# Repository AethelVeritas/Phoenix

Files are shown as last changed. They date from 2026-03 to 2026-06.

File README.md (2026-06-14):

<div align="center">
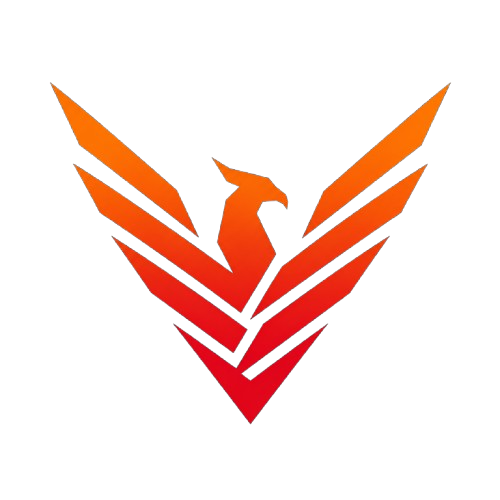
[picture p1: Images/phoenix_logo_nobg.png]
Phoenix Logo
  
  <h1>Phoenix</h1>
</div>

    
Like the mythical phoenix, this printer is reborn from ashes....or rather dust in this case. Phoenix is a high performance makeover of an old Ender 3 V2 Neo, with the end goal decent prints at high speeds, such as 600 mm/s. For a live interactive visualization of the CAD, see the [public Onshape document](https://cad.onshape.com/documents/befe8a04a77aa90d2475bc93/w/b39d9063025263563386822a/e/ff3fb2fc7d22184183b603e8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).

## Features
- **Rigid gantry.** The Phoenix uses a 2020 extrusion bolted into the vertical MGN12H rail carriages and front Z rails instead of the more popular inside Z rail mounting, ensuring better rigidity.
- **Original belted Z attachement style.** Unlike many other belted Z bedslingers, which often have the tensioner on the gantry, this printer uses a separate top mounted Z tensioner, as well as belts attached directly to the motor mount (using a belt and pin system similar to certain CoreXY toolhead carriages) and right behind the 2020 extrusion, which should help with rigidity and tension on the printed gantry parts.
- **AWD 6mm X, with double shear and a MGN12H rail**
- **AWD 9mm Y, with double shear liveshaft idlers, and MGN12H rails**
- **6mm belted Z, with two 4:1 drivetrains.**
- **Reuses a Ender 3 V2 Neo frame**
- **48V for both X and Y**
- **Custom toolhead.** The [Aeolus](https://github.com/AethelVeritas/Aeolus) toolhead has been designed specifically for this printer. The X motor double shear covers have cutouts in order to maximize X travel when using said toolhead. 
- **Custom ebox**, featuring transparent door panels and external TMC5160 drivers. 

<details>
<summary><h2>Gallery</h3></summary>

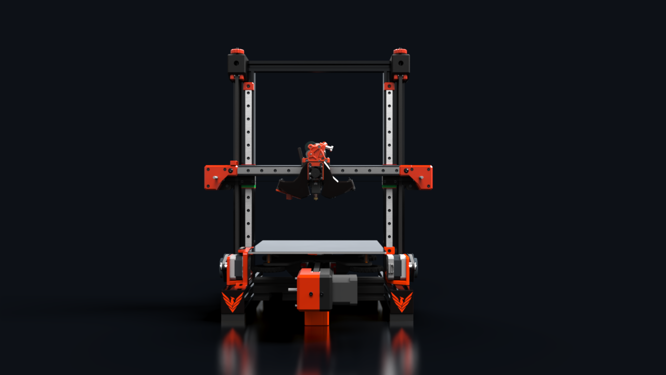
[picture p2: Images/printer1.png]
Printer 1

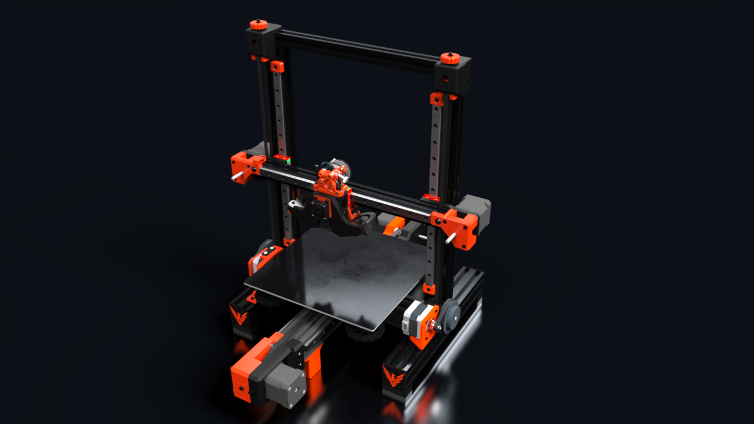
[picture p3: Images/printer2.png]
Printer 2

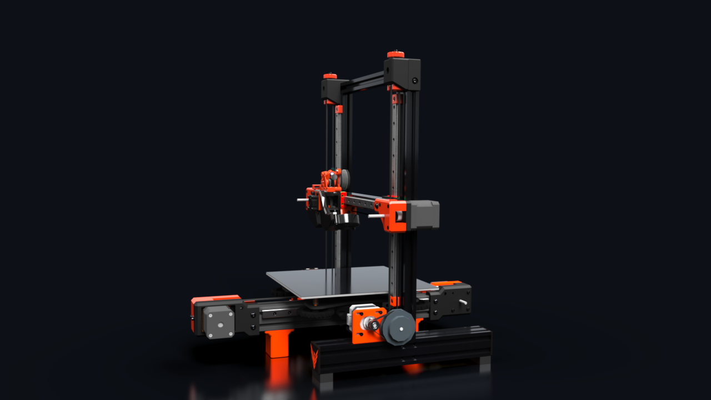
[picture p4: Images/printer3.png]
Printer 3

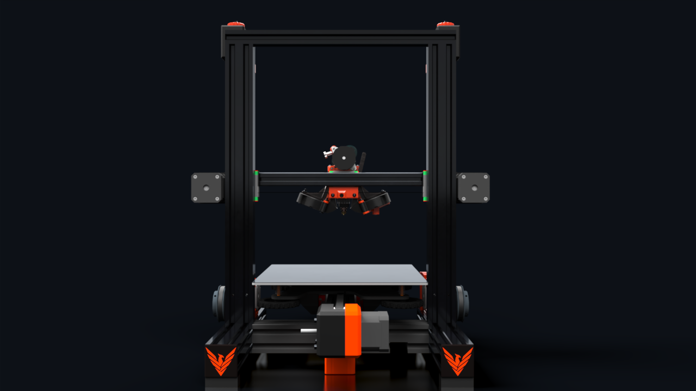
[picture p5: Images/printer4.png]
Printer 4

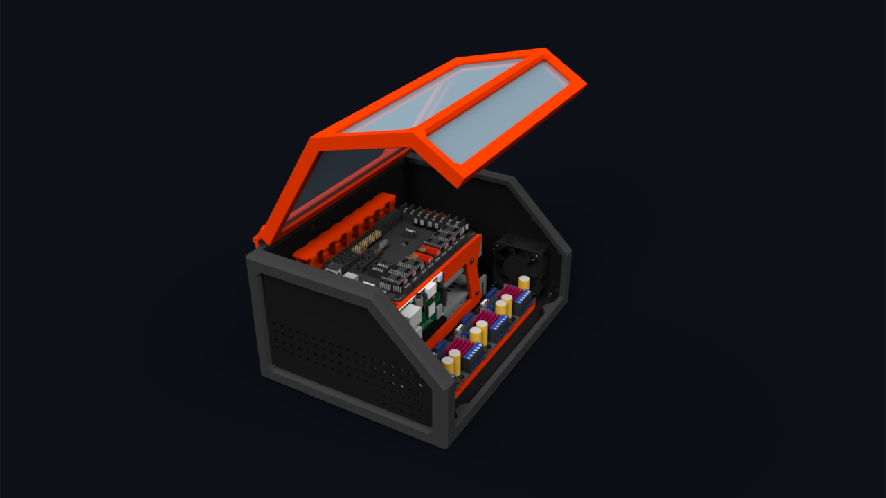
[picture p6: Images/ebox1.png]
EBox 1

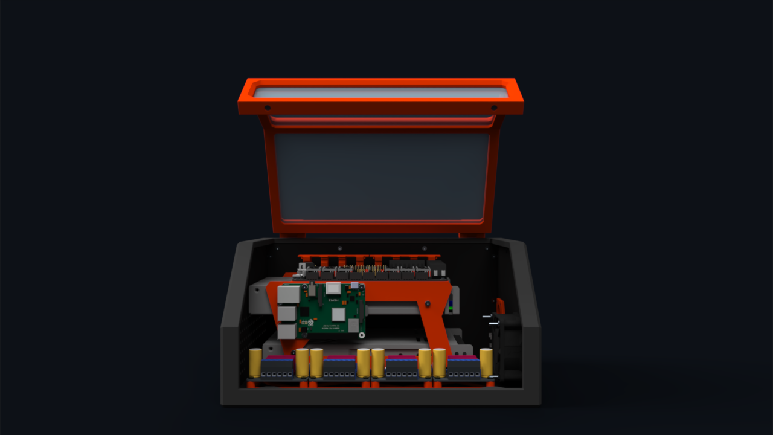
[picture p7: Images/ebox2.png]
EBox 2

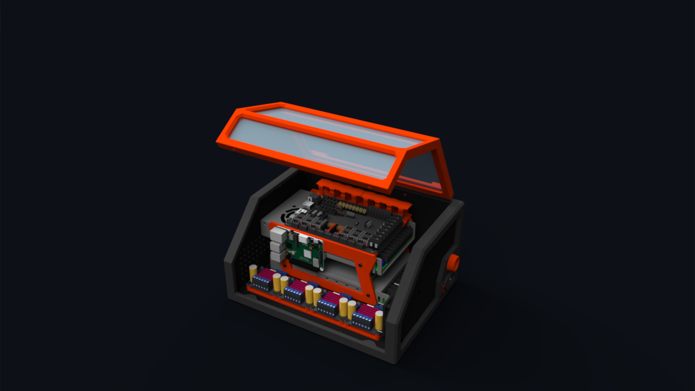
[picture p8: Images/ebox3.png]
EBox 3

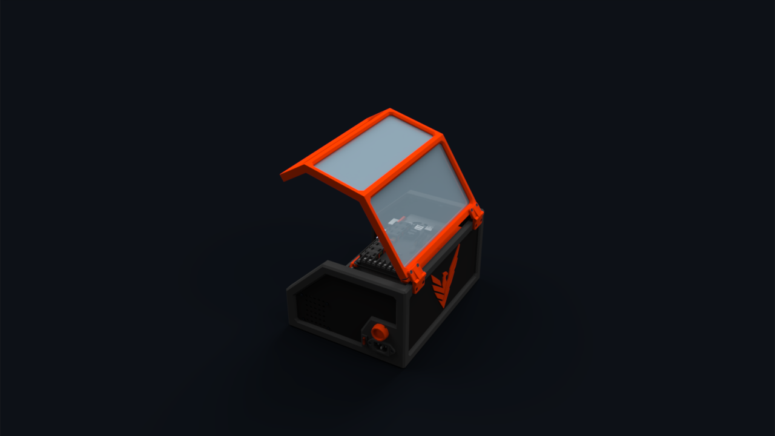
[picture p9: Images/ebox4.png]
EBox 4

</details>

## BOM
The BOM can be found [here](https://docs.google.com/spreadsheets/d/19SDQH5rKj-VOt543ikEq3R2ylwxd--UoErljUox35hg/edit?gid=0#gid=0) or as a BOM.csv. 

## Build Instructions
The whole build should be relatively simple, so just reference the CAD. Wiring the motors, drivers, endstops, probe, hotend, etc in the Octopus Pro should also be pretty simple, as it's mostly just a matter of plug and play. For the ebox wiring, please see [this](/Images/ebox_wiring.png)  

## Why did I make this? 
You may be asking yourself: why even waste money on an Ender/Cartesian bedslinger insted of making a CoreXY? Well CoreXYs are anything but cheap, and while I did initially want to build one (as can be seen in the JOURNAL.md), I quickly realized that it'd be too expensive, which is why I switched to Cartesian as the more affordable option. However, I've done my best to use as many parts that can later be used in a CoreXY build as possible, such as 9mm pulleys, live shaft idlers, F695 flanged bearings and of course, long shaft motors.

## Credits
- [Kevender](https://github.com/kanin2/KevEnder) for the Y carriage and inspiration for the Y motor mounts.
- [LH Stinger](https://github.com/lhndo/LH-Stinger/) for inspiration for the Z drivetrains.
- Ice Cream Factory Discord for all the useful advice they have provided. 
- Hackclub's [Fallout](fallout.hackclub.com) event for the funding. 

### Zine 
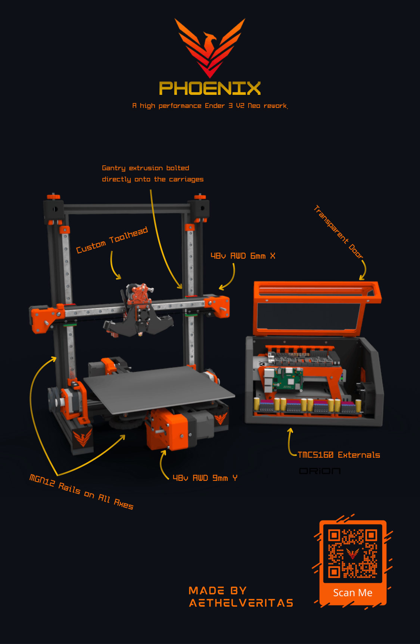
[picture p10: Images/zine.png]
zine


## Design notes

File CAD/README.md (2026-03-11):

You can find the Onshape document [here](https://cad.onshape.com/documents/befe8a04a77aa90d2475bc93/w/b39d9063025263563386822a/e/ff3fb2fc7d22184183b603e8)

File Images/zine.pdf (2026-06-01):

# Phoenix

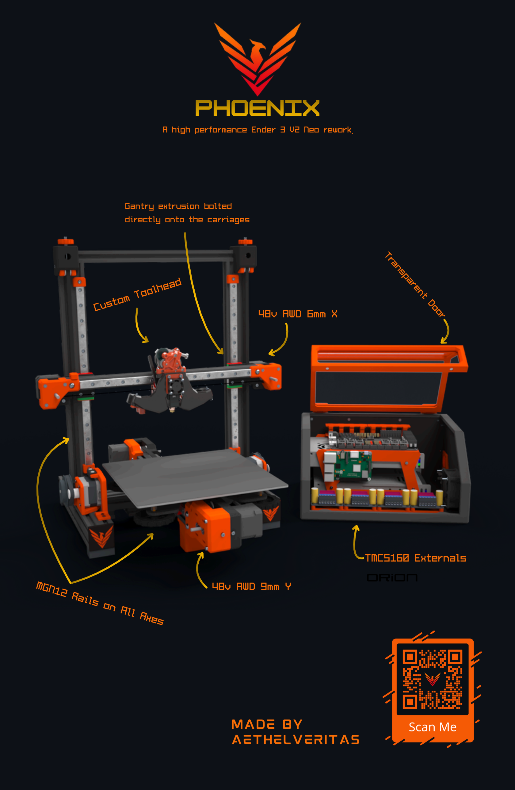
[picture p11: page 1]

Transparent Door

### 48v AWD 6mm X

### 48v AWD 9mm Y

## Custom Toolhead

## MGN12 Rails on All Axes

Gantry extrusion bolted
directly onto the carriages

## Orion

### TMC5160 Externals

Made by
AethelVeritas

A high performance Ender 3 V2 Neo rework.

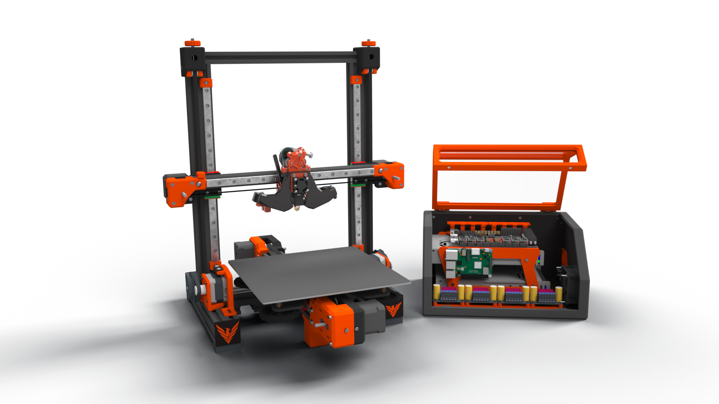
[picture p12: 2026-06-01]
Images/phoenix+ebox_nobg.png

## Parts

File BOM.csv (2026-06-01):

Parts | Price | Status | Supplier Link | Notes
Electronics
350W 24V PSU | Owned
Ender 3V2 Bed | Owned
Ender Nema 17 x 2 | Owned
BTT TMC5160T Plus (no case) x 4 | $80.00 |  | https://www.aliexpress.com/item/1005007805632136.html?curPageLogUid=YRT6Syo2jqKZ&utparam-url=scene%3Asearch|query_from%3A|x_object_id%3A1005007805632136|_p_origin_prod%3A1005007013784064
BTT TMC2209 x 2 | $14.00 |  | https://www.aliexpress.com/item/33028050145.html?curPageLogUid=ziA9pgqQbXmp&utparam-url=scene%3Asearch|query_from%3A|x_object_id%3A33028050145|_p_origin_prod%3A
BTT Octopus Pro H723 V1.1 | $56.00 |  | https://www.aliexpress.com/item/1005003561351349.html?gatewayAdapt=usa2glo4itemAdapt
350W 48V PSU | $20.00 |  | https://www.omc-stepperonline.com/lrs-350-48-mean-well-350w-48vdc-7-3a-115-230vac-enclosed-switching-power-supply-lrs-350-48
17HS19-2504S-H-V1 Steppers | $59.00 |  | https://www.omc-stepperonline.com/4pcs-nema-17-high-temp-stepper-motor-55ncm-77-93oz-in-55mm-round-shaft-insulation-class-h-180c-4-17hs19-2504s-h-v1 | Can get both from one place and save on shipping.
Dragon Ace Volcano PT1000 Hotend | $79.56 |  | https://trianglelab.net/products/dragon-ace%E2%84%A2-hotend?VariantsId=12007 | Already own all the other parts for the toolhead.
Ace Volcano MZE | $9.80 |  | https://trianglelab.net/products/mze%E2%84%A2-dlc-v6-melt-zone-extruder
12mm Cable Sleeve x 5m | $5.20 |  | https://www.aliexpress.com/item/1005007486025295.html?curPageLogUid=pBnRZK9wvyL1&utparam-url=scene%3Asearch|query_from%3A|x_object_id%3A1005007486025295|_p_origin_prod%3A
2 Pin 22 AWG Wire x 10m | $4.80 |  | https://www.aliexpress.com/i/1005009088168543.html | For extending the fan wires.
Stepper Cables 1m x5 | $5.15 |  | https://www.aliexpress.com/i/1005005598759940.html#nav-specification
X endstop | Owned
Y endstop | Owned
Z endstop (probe) | Need to buy |  |  | Will get out of pocket most likely.
Motion
Rails | $87.00 |  | BST | Have to email them to place an order.
Gates 2GT 9mm Belt x 2 m | $7.20 |  | https://trianglelab.net/products/2gt?VariantsId=10440 | tp
Gates 2GT 6mm Belt x 4 m | $9.70 |  | https://trianglelab.net/products/2gt?VariantsId=10435
2GT 9mm 20T Pulley x 6 | $12.20 |  | https://trianglelab.net/products/9mm-20-teeth-aluminum-timing-pulley-belt-pulley?VariantsId=12338 | 6 not 4 because I have two liveshaft idlers, and each uses up 2 pulleys.
2GT 6mm 20T Pullley x 6 | $10.77 |  | https://trianglelab.net/products/black-2gt-20t-6mm-p5?VariantsId=12350
F695 2RS Bearings | $10.50 |  | https://www.aliexpress.com/item/33001186278.html?curPageLogUid=UipmDn4eOVH1&utparam-url=scene%3Asearch|query_from%3A|x_object_id%3A33001186278|_p_origin_prod%3A | Raindew, seen them recommended in Monolith along with Fushi.
5 x 50mm Round Shaft | $7 |  | https://www.aliexpress.com/item/1005007023343232.html?curPageLogUid=ryNRkpVfGAih&utparam-url=scene%3Asearch | For the Z idlers and the Y live shaft idlers. I'll just cut one of them in half for the Z ones.
TL 2GT 6mm 20T Idler | $10.50 |  | https://www.aliexpress.com/item/1005004957508089.html?curPageLogUid=AjU1eNYeN4h1&utparam-url=scene%3Asearch|query_from%3A|x_object_id%3A1005004957508089|_p_origin_prod%3A#nav-specification
2GT 6mm 80T + 188mm Belt Set x 2 | $11.00 |  | https://www.aliexpress.com/item/1005008518079953.html?curPageLogUid=nnHxXq42CUGz&utparam-url=scene%3Asearch|query_from%3A|x_object_id%3A1005008518079953|_p_origin_prod%3A
PTFE Tube x 1m (red) | $2.00 |  | https://trianglelab.net/products/19x4mm-id19mm-od4mm-ptfe-tube-teflonto-for-175mm-filament?VariantsId=12398
Frame/Fasteners
350mm 2020 Extrusion | $9.00 |  | https://www.aliexpress.com/item/1005001604693930.html?curPageLogUid=M0tw1ai2K7Qq&utparam-url=scene%3Asearch
Ender 3V2 Neo Frame | Owned
M3 5 x 4mm Heat inserts x 100 | $9.20 |  | https://www.aliexpress.com/item/4000232858343.html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
M3 x 6mm Countersunk x 100 | $8.00 |  | https://www.aliexpress.com/i/32968616563.html | Ebox
M3 x 8mm Countersunk x 50 | $4.00 |  | https://www.aliexpress.com/i/32968616563.html | Ebox - Only need about 10-20, but these are the cheapest I could find.
M3 x 40mm Countersunk x 50 | $5.80 |  | https://www.aliexpress.com/i/32968616563.html | Again, 50 pieces seem to be about the same price as 10.
M5 x 10mm Buttonhead x 40 | $8.10 |  | https://www.aliexpress.com/item/4000038065691.html?curPageLogUid=Cr3bxbkHbX0Q&utparam-url=scene%3Asearch|query_from%3A|x_object_id%3A4000038065691|_p_origin_prod%3A | Mainly Y-axis, also Z drives.
M5 x 8mm Buttonhead x 20 | $4.00 |  | https://www.aliexpress.com/item/4000038065691.html?curPageLogUid=Cr3bxbkHbX0Q&utparam-url=scene%3Asearch|query_from%3A|x_object_id%3A4000038065691|_p_origin_prod%3A
M5 x 40mm Buttonhead x 20 | $5.50 |  | https://www.aliexpress.com/item/4000038065691.html?curPageLogUid=Cr3bxbkHbX0Q&utparam-url=scene%3Asearch|query_from%3A|x_object_id%3A4000038065691|_p_origin_prod%3A
Square M3 T-Nuts x 100 | $10.50 |  | https://www.aliexpress.com/item/1005003009013919.html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
Drop-in M5 T-Nuts x 50 | $6.30 |  | https://www.aliexpress.com/item/1005003023734101.html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
Drop-in M3 T-Nuts x 20 | $3.60 |  | https://www.aliexpress.com/item/1005003023734101.html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
Black Polycarbonate Sheet x 3mm | Owned |  | https://www.dedeman.ro/ro/placa-hobbycolor-negru-1000-x-500-x-3-mm/p/6022128 | For ebox panels.
Transparent Polycarbonate Sheet x 4mm | Owned |  | https://www.dedeman.ro/ro/placa-hobbyglas-transparent-500-x-250-x-4-mm/p/6019004 | Fo ebox door.
Filament
Devil Design Orange ASA | $29 |  | https://www.diverso.ro/filamente/filament-devil-design-asa-portocaliu-deschis-bright-orange-1kg.html
Torofil Turbofil Black ASA x 2 | $44 |  | https://toro3d.eu/shop/?product=torofil-turbo-asa-black | Need more for the frame + any failed parts.
Shipping
 | $15 |  | OMC-Stepperonline
 | $15 |  | Triangle Labs
 | $14 |  | Toro3D
 | $24 |  | BST
Total: | 678.38

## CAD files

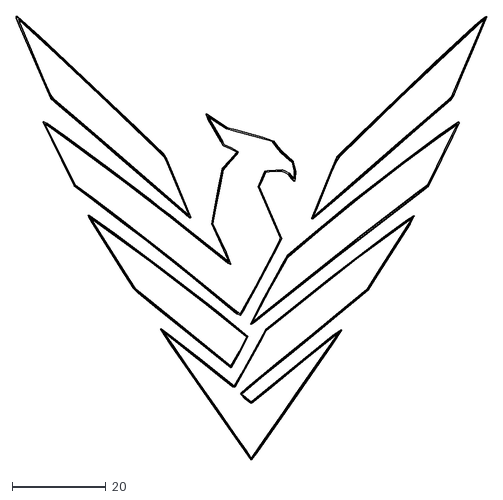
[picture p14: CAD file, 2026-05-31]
Images/phoenix_logo.dxf
100.3 x 94.4

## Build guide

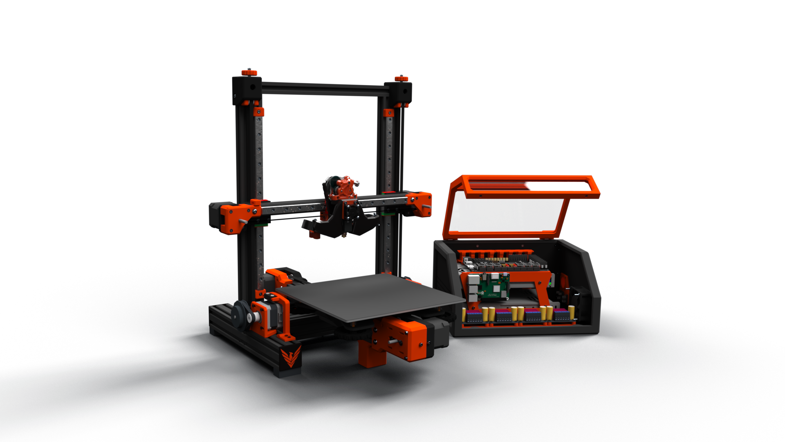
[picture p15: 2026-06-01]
Images/ebox+printer.png

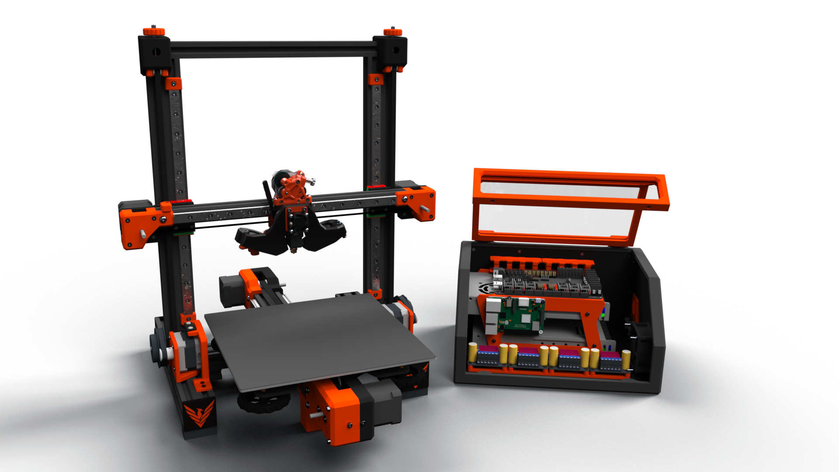
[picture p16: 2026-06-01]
Images/ebox+printer2.png

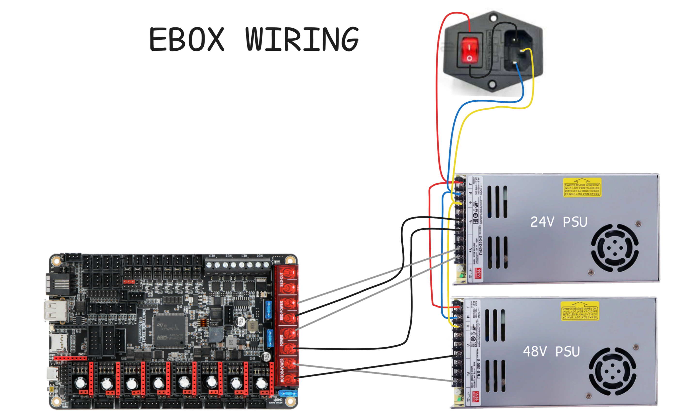
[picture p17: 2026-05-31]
Images/ebox_wiring.png

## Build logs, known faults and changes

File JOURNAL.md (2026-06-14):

# Phoenix — Journal Export

- Exported at: 2026-06-14T18:58:56Z
- Project ID: 1056
- Entries: 32

## Entry 1
- ID: 4875
- Author: AethelVeritas
- Created At: 2025-10-22T09:37:00Z

### Content

I started off by basically just doing a lot of browsing to try and find out what I want to make.
The closest printer I found to what I want to build would be the [Salad Fork](https://github.com/PrintersForAnts/Salad_Fork?tab=readme-ov-file) by [3DPrintersforAnts](https://3dprintersforants.com/). It's basically a shrunk down Voron Trident.


I'm definitely using 2020 extrusions instead of the 1515 used here though.

Pandora's Box (also by 3DPforAnts) looked very interesting, and I would love to attempt to build something like that, but having a belted z-xis would be too complicated, so I'll just stick to leadscrews for my first build. Speaking of the z-axis, I was considering of using one motor for all three leadscrews and using a timing belt like the X1C and the [Anicept Vex](https://github.com/invictus-anic3tus/anicept-vex/tree/main?tab=readme-ov-file) use because it's cheaper, but after asking around and looking at other printers I realized that z-tilt is too valuable to sacrifice. Oh and @Renovic on the HC slack provided an extremely helpful explanation comparing the different types of z-axis setups for fixed gantries:

> Motion type
Leadscrew
Sometimes can lead to z wobble
Integrated leadscrew are usually better since some couplers are a bit springy
Usually the simplest option
Look at trident
Belts
You almost always need a gear reduction
using a 60t and 16/20t pulley with 188t belt is common
Some use nema 17 planetary gearboxes but its sometimes expesive and usually has backlash
Highest gear reduction is worm, but thats also somewhat expensive
If its a really small printer(like v0 or slightly larger) you can get away with a 16t pulley or using bmg gears for a reduction
Look at 2.4 z drive or k3 z
Number of z motors/points
Triple Z
Pretty common because 3 points define a plane and allows for bed tramming with 3 motors
You can do 3 leadscrews without 3 seperate motors by using a timing belt to link them together, this is better than controlling a multiple steppers with the same driver
Double Z
Can be worse that triple Z, but its often better for packaging and usually used with linear rods on Z
Single Z
Only really used for small beds, you need to make the bed carriage really stiff for the bed to not bend or bounce

## Entry 2
- ID: 4876
- Author: AethelVeritas
- Created At: 2025-11-03T15:52:00Z

### Content

I mostly did toolhead research. I've decided I'll use the Xol Carriage from the Xol Toolhead, as well as the A4T toolhead, both of which seem really good. I did some research regarding on how to mount the belts to the carriage, and yeah the Archetype clips seem to be the best. For custom toolhead carriages, it's recommend to wrap the belts around some pins, and then make sure 3-4 teeth interlock. Seems to be the most painless way of doing it. I've decided I'm going to use a 20150 axial fan and two 4010 blower fans. That way, if my toolhead sucks (which it probably will), I can reuse the parts to make an A4T or Xol (another reason to use the Xol carriage). I'm also going to use the TZ 2.0 V6 hotend, as it's cheap and decent. I spent a lot of time trying to understand different toolheads and their creator's design choices. But I've now decided, after almost two days of research and browsing that I'll like place the A4T toolhead in the assembly, design the gantry, frame, and everything to that, and then finally make a placeholder/basic toolhead. Toolheads are difficult to make, but can easily be replaced with existing designs. Gantries, frames, and everything else not so much. 

Here are some great resources/references I've found:

https://github.com/Armchair-Heavy-Industries/A4T/tree/main
https://github.com/Armchair-Heavy-Industries/Xol-Toolhead
https://github.com/SartorialGrunt0/Awesome-Toolheads
https://github.com/PrintersForAnts/Voron-Construct



## Entry 3
- ID: 4877
- Author: AethelVeritas
- Created At: 2025-11-17T22:44:00Z

### Content

So... for the past week or two I've been doing some more research. Scoured Discords, Reddit, and Googled. I can't come up with an idea for doing a new/original idea to make the monolith gantry unique, as I was instructed on the slack. I thought about doing diagonally braced 1515 frame and adapting the monolith to that, then using panels like the monolith zero but with a printed gantry, then 12 mm belts, and then 3030 extrusions, but none made sense/would fit my budget. Turns out 3030s are pointless if you use a bed with a smaller volume than 250 mm, 1515s are pointless for obvious reasons (2020s exist), and using aluminum side panels is obviously ridiculously expensive. I've come to the conclusion that there is no way I can adapt the monolith gantry to be original while still fitting inside the budget and using a 2020 frame. So, I've decided I'll just use the trident and monolith gantries hardware as a reference and build a gantry from scratch without looking at any other ones (as much as possible, that is). That way, I'll have a good learning experience as well as a fail safe: if my gantry does not perform well I can just buy some more parts out of pocket and adapt it to a monolith. Problem solved! 

The hours I've spent looking at the monolith's cad trying to figure out improvements are ridiculous lol.

## Entry 4
- ID: 4878
- Author: AethelVeritas
- Created At: 2025-11-20T08:23:00Z

### Content

[Something about belt tension too much for not live shaft idlers](https://youtu.be/4XGGuhTlJaw?t=152)

I think I've come up with an idea on how to use a monolith style gantry without directly copying it, but reverse engineering it with purpose in mind, as instructed by @Samliu on Slack! So what I'm think is that I'll move the motors *outside* of the frame, so like just push them back. I'm going to have an electronics backpack, so it won't look ugly or anything. I can also use adjustable sliding motor mounts as the belt tensioners, which is pretty neat, even though I liked the design of the Monolith tensioners. That way, if I ever try to print HT (high temp materials, such as PEEK or Nylon) and I want to make a good chamber, the motors will not heat up! Plus I'd have a little bit more Y space in the gantry, which would be really useful if I want to add a toolchanger mod later on. 


Ok I'm scrapping the whole core-xy idea, which is sad, as I've just found a good idea for the gantry. I've done even more research, and I can't make it as good as I want within $400 usd + 100 which I can pay out of pocket, so yeah. As with Tanqish, people in both the Monolith and Ice Cream Factory Discord servers told me it's not really possible: a decent build would be at around $700. So here's what I'll do: I'll try and design an Idex cartesian printer using $400 USD budget. I can reuse a bunch of the extrusions from my Ender 3 V2 Neo, as well as the bed, bed carriage, and worse case scenario, a motor for the z-axis. The key here is that while trying to make a good printer that fits in the budget *I try and use parts that I can reuse in a corexy later*. So for example motors that can be double-sheared, 9mm belts, idlers, and pulleys, a good-ish extruder, a CAN board maybe, good drivers and mainboard, etc. I'll use cheap hotends because I need to get two, but the protxtruder is cheap and should work for both this and a future corexy. That way, once I build this printer and get it working, if I design a corexy I'll have a much higher chance of getting sponsors for it, and it might actually be doable at a following hackclub event. 

New Design Constraints: 
- Use as many reusable parts as possible. I'll reference the Monolith gantry BOM and see if I can use as many of the pulleys and stuff used there in my parts. 
- A few high quality parts are better than more medium-low quality parts. Why? Well because for a bedslinger IDEX I don't mind if I have like good motors but a heavy bed and thus can't reach high accels, because the main feature will be the IDEX. But if I reuse those motors later on in a corexy I'd much rather have them be good. 
- Try to use as many of the parts from the Ender 3 V2 Neo I have without compromising on performance too much. I'm most certainly going to use the existing 4040 Y axis extrusion, as well as the two side 4040s. That way I'll just need like maybe a front 4020 to connect them together + some 4020s or something for the z axis (I might even reuse the existing ones, though I doubt it: depends on where I mount the rails). Actually many designs only use three extrusions for the bottom, so like an H shape. No need to make a square most likely. 
- Decent print speeds, something like 300 mm/s^2 would be great.

I can get two 290 mm and one 350 mm 4040, two 400 mm 4020s, one 330 mm and one 345 mm 2020. Damn 2020s are smaller than I assumed: I thought they were 1515s at first. Ok so I need space for the two toolheads +  the bed. The bed is 235 mm, and the A4T toolhead cowling is about 69, so 235 + 80 (to be safe) x 2...wait hold on I can park the toolheads like over at least part of the bottom 4040s that sustain the Z axis. I'll have to figure out the x-axis first. I'm going to use MGN12H rails for both the gantry as well as most likely both sides of the bed.

[The steppers I'll probably use ](https://www.omc-stepperonline.com/4pcs-nema-17-high-temp-stepper-motor-55ncm-77-93oz-in-55mm-round-shaft-insulation-class-h-180c-4-17hs19-2504s-h-v1)
I'll most likely use a BTT Octopus Pro or something similar. On Ali it's around 85 usd with stepper drivers included. I have to see if I need some for the extruders as well, + CAN and shit.
Protoxtruder would be about $30 a pop. Fans from what I can tell would cost about $25 per toolhead. An BTT EBB 36 board is 15-18. Frame might be $40 USD max including shipping as I only need two longer 2020s and a 4040. 

two skr picos are like 22 per piece

## Entry 5
- ID: 4879
- Author: AethelVeritas
- Created At: 2025-11-23T22:21:00Z

### Content



Soo...busy two days. Did a lot of stuff. I did some more research (yes, I'm a perfectionist, I'll research and double-check like crazy), and after some back and forth in the Ice Cream factory Discord, I've decided that I'll do a [Ratrig V-Cast](https://cad.onshape.com/documents/d85f63cb1dd00c47513242ef/w/078df75818db59591633b24e/e/6d79b98fe36ffb8e62f69638) style X gantry. This is after I tried to make a like an offset (relative to the 2020 extrusion) idler tensioner and motor mount. 





Thing is that if I did this like this, then because of the extra material needed for the tensioner, the idler and thus the belt paths would be off-center relative to the center of the 2020 extrusion. Wasted several hours on this, but yeah as I said I scrapped this design.

The next several hours were spent iterating on a motor mount inspired by the V-Cast's, but from scratch and improved to support double shear as well as live shaft idlers. Here's a what I came up with (to be refined tomorrow): 



The tolerances for some of the parts such as the bearings and shafts are inspired from the monolith gantry. Also I spent like another hour figuring out how to use Super Derive, which is an amazing Featurescript that's basically the Derived feature but on steroids, allowing you to remove, add, and intersect your derived parts,even several at once. Now what I did was I made kind of like a bearing with tolerances, and then used said feature to subtract it for the top two bearings "holes" of the gray part. This saved me quite some time and sketching. Well technically I lost time because I had to troubleshoot the feature, but now that I know how to use it it's going to save a lot of time, as I'll have to use more of the same bearings and heat inserts in other parts of the printer. Also dang the hours are flying! Can't believe how much time is wasted on searching and finding dimensions as compared to CAD. Over 50 hours already :'(

## Entry 6
- ID: 4880
- Author: AethelVeritas
- Created At: 2025-11-24T16:07:00Z

### Content





Finished doing the assembly for the x gantry, and refined the motor mounts+ joints a bit more. Took some time because I had to manually import parts, readjust the printed part to fit screws (using 35 mm as the part itself is 31 mm now and the motor + tnut screw holes are about 4mm), and learn how to make better assemblies. I manually imported the screws and bolts only to realize that the standard content library did in fact contain the lengths I was looking for but under ISO section, not DIN. I'm dumb. Also used the "Frame" tool to generate the 2020 extrusion.
Oh and I've also decided to use the my main task app, SuperProductivity, to track how much time I spent on what on the project.  


Should have done this from the start tbh.

## Entry 7
- ID: 4881
- Author: AethelVeritas
- Created At: 2025-11-29T09:45:00Z

### Content



Soo...this was a lot harder than I expected and took me an abnormal amount of time to design. At first, I thought I could get away with using a tensioner on the bed, similarly to what the lh-stinger does and what Mitsubishi makes does in his Ender 3 upgrade video. This would have simplified the motor mounts, as I would only have to design one and mirror it, a much simpler part at that. But the Lh-stinger uses a custom carbon fiber bed, which brings the weight down from the about 1.8 kg of the original bed to about 700-900 grams, so it can afford a few extra grams for the tensioner on the bed. I cannot afford such a bed, and it's not worth it for my usecase, so yeah motor tensioner it is. The main two projects I derived my inspiration from are [Kevender](https://github.com/kanin2/KevEnder/tree/main) and this [AWD Ender 3 mod](https://github.com/CarnageMarkus/ender-3-pro-awd-y). Even though I kind of liked how AWD Ender 3 mod made use of the pre-tapped screw holes in the standard 350 mm 4040 bed extrusion, the Kevender seemed more well-thought and practical, so most of my inspiration/references were derived from that. Deadlock from the Ice Cream Factory Discord provided me with a great formula regarding how how long do I need to tensioner to tension:
>You want the tensioner to cover at 2% belt length + whatever wiggle room you want for easy installation.
If you're tensioning on an idler or pulley, it's halved since 180° doubles it
So assuming a motor tensioner, 1000 mm belt length and 4 mm leeway you'd get 12 mm

But seeing this has kind of made me worried regarding the toolhead tensioners I'll be using: I don't know if I can fit about 12 mm of tensioner travel in the toolhead without it disturbing the COM and weight too much and besides that I'll also have a longer belt length. I guess I'll cross that hill when I get to it. 

### Nov 26-27
This was basically a failed attempt. 


I think I spent like 6 hours on this in total, and yeah the way I went about it was crappy as hell. My biggest mistake was that I did not make a mental "feature timeline" of sorts before starting, and as a result there were a lot of unnecessary unoptimized features and sketches. From now on, before trying to make a new part (especially if it's inspired/derived from an already existing one) I'll first try and write down or just mentally note how I'll go about it. Things like what will the main sketch contain? How can I make it as parametric as possible? What tolerances might need adjusting, and do I make variables for those to help with said adjusting? In what order will I make the features? Should I use offset for a feature or just use a new sketch that'll be placed on the previous feature and thus relative to it?  Things like that. 

## Nov 27-28
Started a new part. I've decided that I'll reference as much of Kevin's design as possible in order to save time regarding screw positioning and tolerances, but I'll adapt it a bit because I'm using 9mm belts and live shaft idlers, as well as 55mm motor shafts, all of which interfere quite a bit with Kevin's current part. 




So these are basically my new versions. I made a slot for the longer shaft to pass through, added flanged bearings for double shear even though normal bearings would have probably been easier (so that if need be I can reuse them for monolith later on), used 4 short screws and 2 long external ones instead of 2 short and 2 long like the Kevender used for the sliding motor mount, and added space for a dehubbed 20T 9mm pulley (and double sheared and aligned that, obviously) and yeah. 




I'm a bit worried (look at the last pic) for the bearing to like rub against the white outer part, but if needs be I can adjust that later and either make a small detachable lid of sorts or just embed the bearing deeper in. 

And then obviously I also made a pretty simple back motor mount. 
And I also started working on the full y-axis assembly. I'm using a subassembly for the front motor mount tensioner, and I'll probably add screws and motors to the back mount as well just for the looks, but besides that all that remains is to add the bed (which is going to be the standard Ender 3 bed with a mount for the two parallel MGN12H rails). 
In total, I think I spent about 10 hours on this. Did like a 3h spree on the night of the 27th, then several hours the next morning, and another 4h on the night of the 28th.

## Entry 8
- ID: 4882
- Author: AethelVeritas
- Created At: 2026-01-02T08:10:00Z

### Content

One of the things I'm worried the most regarding the Z axis is the gantry crashing into the bed if I do belted z. At first, I hoped I could get away with how the LH-Stinger does it: the gear reductiong + cogging toqrue suffice to at least dampen the gantry's fall. With the help from some people in the Ice Cream Factory discord, I realized that it would not be enough:
>For class B insulation hybrid steppers the detent torque is usually around 5% of the holding torque 5% of 400 mNm is 20 nNm 20 mNm × gearing / efficiency ≈ 85 mNm With 20T final pulley (assumed) you get 85 mNm / pitch radius ≈ 13 N 1,3 kg per stepper, while with a safety ratio you'd want at least 3,5 kg per stepper

This clearly wouldn't work for my estimated gantry weight of 4 kg. Did some more research and I found that [Z motor brakes](https://www.formbot3d.com/products/z-motor-brake) are a thing, but they are not cheap.  Someone suggested BMG Z, and Renovic also said that >
>"I'm using creality stock x motors for z with a 4:1 gearing. Your gantry is likely only 300g more from the extra toolhead and axis length, but I have aluminum plates and a 120mm fan mounted to the x axis. So if you use better motors or higher gearing you will likely be fine"

But Ocho and Deadlock said that 10:1 geared would hold about 1.2 kg before drop, and that the best solution is constant force springs. For now I'll try to just make the Z-axis and worry about adding springs later. 

For the belt tensioner, I want the pulley+motor to move about 6mm, using the formula provided by Deadlock mentioned in my previous post. I'm going to be using a 80t pulley and a 188mm belt, like the LH-Stinger.



Ok so here's what I've got so far. Obviously very LH-Stinger inspired (black part is from the latter for comparison)


I'm using F695 flanged bearings though (because I want to be able to reuse them for the monolith if I ever make one), and I'll be mounting it differently. As you can see, the LH-Stinger uses two holes right beneath the pulley for two M3 x 22 screws, as well as another one right in front of the motor. I'm using obviously different frame, so that's not going to work for me. What I'll do is I'll use one M5 underneath the pulley, for the like Y-axis extrusion, and then another one in front somewhere for the X-axis extrusion. That way it'll be centered but still solid. 

## 26th 
Ok....long time no do nothing. Had some family stuff going on + exams, so I haven't really gotten around to working on it. Let's see if I can somehow speedrun the Z, electronics, toolhead, and BOM in 6 days lol. 

So, if I want to add another screw right beneath/in front of the 80t pulley I'll need to lift the whole thing up a bit, which isn't really convenient, because that'll use more material + longer screws. I've got 50 mms from the extrusion to the start of the Z-rail, and the part is currently 43 mm tall, so I do have some space left but yeah. Why use more material if it it is not necessary. Plus a protruding "tongue" for the screw emerging from underneath the 80t would kind of be a weak point, as it's only connected to the part on one side. Not that it matters much, but why not stick to good design principles for practice at least.



Just realized that using an m5 screw like I intended would result in this abomination, as this slot is much closer to the vertical extrusion than I thought. Might have to just do like a 2-3 M3 screws after all. Anddd an M3 wouldn't fit either. Argghhhhh! I might have to try and like screw it in the vertical extrusion. Not optimal, but yeah.

Oh by the way I got a quote about how much the rails would cost from Brazuka over from the Monolith discord.  
>2x 350 MGN12C - US$25,80 2x 300 MGN12H - US$23,20 1x 400 MGN12C - US$17,60 (2 carriages) around 24 shipping

This if for the in-house BST rails, not even airtacs/hiwin... I'm screwed.

Ran into another problem:

When trying to edit the mate that connects the gantry to the rail block, I get a ton of over-defined errors. Onshape mates are weird...I had to redo a large part of the assembly.

## Entry 9
- ID: 4883
- Author: AethelVeritas
- Created At: 2026-01-05T19:50:00Z

### Content

I'm switching direction. Again. It's annoying, and I really wanted to build an IDEX, but with a new law being introduced here that adds a tax for any package shipped from outside of the EU I just can't do it anymore. Even if this wouldn't have existed, I was still pushing limits with the budget. I would have payed at least $150 out of pocket, and just for a cartesian IDEX, especially a first printer design, I don't think I'd be willing to pay $200 (which is what I would have most likely had to pay given an error margin). Instead, I'll try and focus on just a simple Cartesian bed slinger. My Ender 3v2 Neo is still collecting dust, and I'd like to put it to some use. With the IDEX I would have reused some parts from it, such as several extrusions, the PSU and the motors for the Z, and I'd like to use even more parts for this new build. Ahh speaking of, I'll have to come up with a new name now. Orthrus was an amazing name for an IDEX (Orthrus in Greek mythology is Cerberus's two-headed brother by the way), but for just a bedslinger it won't be appropriate. I'll worry about that later. I can reuse all of the CAD and researched parts from the IDEX for this, except the X gantry CAD, obviously. The Z will also probably need some more modifications. I still want to keep trying to use as many reusable parts as possible, with the reference being the Monolith gantry, as before. If I want to build another printer in the future or if this one doesn't work out as I expected there's no point in parts going to waste/buying new ones.

But this time I'm using my damn brain and building a more detailed tentative BOM first. I'll still be using the BTT Octopus Pro, as it's a good mainboard for future builds as well, and most importantly it can run 48v, and I'll definitely be wanting a 48v PSU now. The board + four TMC5160T Pro drivers is about a hundred bucks on Ali. I think I'll use the same motors from steppers-online, as I haven't really seen another decent option that is long enough for double-shear without costing an arm and a leg (LDO Speedy Power HTs I'm looking at you lol). I might use 9 mm belts for the X now, seeing that I don't have to worry about two overlapping belt paths. Still going to stick with the Protoxtruder for obvious reasons (cheap-ish + good), but I'll be using a different hotend hopefully. 

Did some research on the PSU, which seemed really confusing at first. Max amps for the HT 1.8 deg Nema 17 55Ncm is 2.5A, so 48V * 2.5A * 4 motors = 480W. Ok I'm dumb ignore that. After some blindly stumbling across random PSU info on the web I did some digging in the Ice Cream Factory server which payed off, as usual. Deadlock gave [this](https://discord.com/channels/733350014805344377/733350015384420396/1246963470403108864) formula to calculate wattage:
>Estimate (a bit low but a starting point) is P = ((U_induced_RMS × I_RMS) + (I_RMS² × R_coil)) × 2 
>U_induced_RMS you can calculate from speed, current, inductance and steps per rev

But this seems a bit overkill for just a rough estimate, and I don't have the brain power to sit down and do the math right now. So after some more research seems many people use a 200W 48V just fine, including Brazuka (who gave me the rail quotes) from the Monolith Discord. That seems to be for a 2WD monolith gantry though.... Ah dang it I'll deal with it later: I don't need exact numbers for a rough price estimate. For now, I've found some Meanwell PSUs sold by steppers-online, the same place I plan to get my motors from, so I'll save on shipping.

Moving on to the toolhead. Probably should have started with this to be honest. Gonna use a klicky probe (obviously), Protoxtruder 2.0, and I was thinking the Peopoly Lancer Long, until I realized that with shipping that would be about $70. Now I have to find a new hotend. Never mind that the toolhead is on hold again. Probably going to use the Dragon Ace or as Evan suggested on the slack a TZ 2.0 V6 with a Trianglelabs MZE (meltzone extender). But still have to do some more asking around.

I'll have to rework the Z unfortunately, because if I keep the standard frame configuration then the lower motor mounts wouldn't fit under the belts. Fortunately, I don't have to start completely from scratch. The orientation of the pulleys will look roughly like [this](https://www.printables.com/model/932314-belted-ender-by-squirrelf#preview.R1zwE), so basically just flipping the motor mount across the Y axis. This remodeling is a lot easier as I already have experience from the first Z mount attempt. Here I made a version of my last version of the IDEX Z mount so I can always revert to it, then went to the base motor sketch and flipped across the center, and also the whole sketch better and clearer (even though it doesn't look like it haha).





Oh and I started tracking what I did again. 


## Entry 10
- ID: 4884
- Author: AethelVeritas
- Created At: 2026-01-07T22:42:00Z

### Content

My God am I dumb!!! So I've been struggling with like getting the proper angle and mouse position to select what I want to add a mate connector to for so long, and now in frustration I just googled it, and turns out that once like all the white possible mate points appear on the screen you can just hold shift and select which one you want. 

So I've been looking the BOM to see where I could make a compromise or something because I'm like already over-budget with the shipping and all, and I realized that even though AWD X sounds nice, I don't really need it. Like the X gantry has a relatively short belt path and the LH-Stinger goes insanely fast and only uses one motor. The main limiting factor will obviously be the bed, not the X axis. Well a motor is 14 USD, so I guess I'll see. Might just buy a set of 4 to save $7 off of one and just pay that out of pocket.

Started working on the X gantry. So I have a dilemma: I'd  like to use a 9mm belt even though it's overkill as I'd have multiple reusable parts left if I ever dismantle this thing and because a 9mm will obviously be stiffer. But, that would mean I have to run like both 'halves/lines' of the belt underneath the 2020 gantry extrusion, which is not ideal for the COM of the toolhead. So, I guess I'll just settle on doing a AWD 6mm X which will still be overkill but a bit easier to work with. Anyway, the X is not going to be the limiting factor in any case, but rather the heavy bed + carriage of the Y.  I'll still do a toolhead tensioner like the LH-Stinger even though I'm doing IDEX anymore because I really can't think of another good alternative for AWD X: I really don't want to add any weakness by trying to tension one of the motors.

I don't know if I'll do this now, but later on I definitely want to make a shape similar to how the Monolith gantry does it that I can subtract for press fit bearings. I have one for F965 bearings currently, but well it's not very "press fit optimized".  So basically a shape that's the negative of this:


12 sided polygon instead of a circle (similar dimensions, obviously), so it works better for press fit. I'll probably just take a part from the Monolith and then boolean and cut up a shape I can then use to remove multiple times from parts I want to add bearings to. 

So after several hours of measuring and designing, this is the very rough part I came up with:




While this does in fact seem like a rigid and good part, and while I do like the added rigidity given by making the top green part bolt onto the extrusion just like the back grey part, I've just realized that this will actually make me lose quite a bit of X travel, and make the placement of a Klicky or nozzle brush rather impossible. So, I'll have to chop off some of the green part. The back grey part shouldn't interfere with the toolhead if I design it properly, as it should be able to move like in front of it. Arggh. The amount of things/design constraints I discover about only after designing something is hilarious. 


Regarding press fit bearings: I don't know if this'll hold up to be honest. Hopefully the tolerances will be tight enough. If not I guess I'll just make it be on outside, but that'll make everything much harder to print. 

This isn't perfect, but it should do for now. I'll have to add an endstop switch mount and the screws in the assembly later once I get a rough draft of everything. 


Now let's deal with the elephant in the room: the toolhead. Renovic over on the Slack said he got to 30K X accel and 19k Y with v-wheels, AWD X and Y and a LH-Stinger toolhead modifed for the Peopoly Lancer Long hotend. I'll be referencing the LH-Stinger toolhead a lot for general measurements probably, especially for the belt tensioner (that the EVA toolhead series). Als I really like the Xol and A4T, so I might reference some of those too. But firstly I most decide on the hotend I'll use, and then what fans, so 5015, 4010s, or those big square turbos that look insanely cool but eat up a ton of X space (saw [this using them](https://github.com/WV-design/Trinity-toolhead/) in the Monolith Discord and I think it looks so nice and minimal). But as I have my motors shifted a bit downward for a decent belt path it'll interfere with them most likely if I use the turbos. I think they are 3612s.

>PTC heaters are the most cost effective heaters and also the most safe thanks to them increasing in resistance. There are two sub types of PTC heaters we see: Rectangular and circular PTC heaters. Circular PTC heaters are known for breaking over time due to thermal expansion applying pressure on the heaters circular face. Circular heaters are not the correct choice because of this.
>thermistor placement is 1 of the critical choices in hotends. Due to the nature of hotends, there will always be more losses at the bottom of hotends due to part cooling fans blowing at nozzles. Having the thermistor as close as possible to the nozzle reduces the effect/ time it takes for the thermistor to see change in tempature. Software is 1 way that this issue is beingg circumvented to some extent with [https://github.com/KalicoCrew/kalico/pull/333](https://github.com/KalicoCrew/kalico/pull/333 "https://github.com/KalicoCrew/kalico/pull/333") using [https://marlinfw.org/docs/features/model_predictive_control.html](https://marlinfw.org/docs/features/model_predictive_control.html "https://marlinfw.org/docs/features/model_predictive_control.html")

Some info by Burgo that I scrapped from the rather messy hotend info thread in the knowledge-depot of the Ice Cream Factory discord server. After some more digging through the long and tedious messages of multiple Discord servers I have come to the conclusion that I cannot do better than get a Dragon Ace lol. Burgo recommended it, Renovic recommended it, the A4T toolhead setup recommends it, so yeah. $70 USD but such is life. Definitely going for the PT100 version, as I want to be able to print at higher temperatures in the future if I ever reuse the damn thing. Tomorrow I have to deal with fans, but enough for today (yes I know I'm a slow worker, I do a lot of research).


Never mind that I'm doing more fan research now. https://www.youtube.com/watch?v=mxb71Ndg6tY Found this video, seems useful. According to the latter axial fans (4010s, 4020s) move a high volume of air at high pressure, and the airflow is parallel to the fan axis, while radial fans (5015s) move a low volume of air at high pressure, and the airflow is perpendicular to the fan axis. 4010s are not designed to force air through small ducts, and require a better understanding of fluid dynamics to make them good.  I just asked in the Ice Cream Factory Discord regarding fans, and CarVac shared a bunch of information:
>4010 is for compactness. notice that stinger is a bedslinger and uses that to spread the fans wide so it makes the most of 5015s. there are narrow mouth and widemouth 5015s, the widemouths are often on oem chinese 3d printers. 4020 is similarish to 5015, that's on prusa mk4s and core one. dual 3628 moves high volumes of air, good for fast printing of large objects but it's not as good at point cooling for bridges or tiny objects (speedboating). And ratrig uses a single 4028. The real high performance cooling is done by outsourcing aka cpap.
>CFD is almost completely foor part cooling duct design. Why not simply do test prints? Way faster. And the part geometry under hte nozzle matters, and the Colorful Flow Diagrams don't tell you what cooling is. Also cfd isn't informing you much besides "is the flow going in this general direction", it doesn't know how flow exits the fan nozzle (more on the outside, less on the inside), you and therefore it won't know your blower's pressure/flow curve...it's really not hard to make a solidly functional duct with a little trial and error. Making _the best_ duct for insane printing speeds is another story.But cfd isn't helping at either end: both are highly dependent on trial and error. 
>
>Especially for a bedslinger? that's easy you only have to worry about two things: aim and nozzle area. Smaller nozzles are better with modest (6500 rpm) 5015s because they restrict more, generate more pressure, and convert that pressure into flow velocity but the same nozzle will limit the cooling capacity of a faster (8500+ rpm 5015) fan because above a certain flow speed your cooling doesn't get thaaat much better, while you can benefit from a larger area being cooled with sufficient-velocity air. And aim? aim for just below the hotend nozzle, and not 180° opposed from its paired part cooling duct.

Oh and I'll probably get two 9733 fans in the future and print the LH stinger sheet cooling. Seems it helps a lot, and two fans are like $15-20, but I don't have the time or knowledge to design sheeting cooling now as well.
On a random note I'm thinking of using the drill press (if it still works) to remove more mass from the bed carriage.

## Entry 11
- ID: 4885
- Author: AethelVeritas
- Created At: 2026-01-11T07:00:00Z

### Content

So. Ducts. I'm dead :)) 
Found [this](https://www.youtube.com/watch?v=YijwkQCOBEA). Summary:
- Golden rule: Narrow ducts gradually! Don't narrow a duct by more than 11 degrees.
- Every fan has a tipping point, after which if you narrow the duct more you start loosing pressure instead of gaining it as it chokes the airflow.
- You need to find this ratio: outlet_area/input_area x 100 = final reduction 100%. The you have to do test prints and see (with water or cardboard) at what point does the duct start to choke the airflow.
- The easiest way to start designing a duct is place your start and end sections and then work from that to the middle.
- The duct *must* be as smooth as possible. Try to use big mellow curves, avoid sharp angles/curves.
- Minimize the duct perimeter as much as possible. The perfect duct shape is a circle.
- The shortest possible duct will under-perform compared to a longer duct that has smoother transitions. 
- Don't cut/transition to the final outlet cross-section too soon, as large ducts are more efficient than small ones.
- Aim the airflow so that they just clip the nozzle. The actual airstreams will obviously spread out differently depending on where they intersect with what you are printing, bu this is a good practice. 
- If possible, end the ducts with a short straight or slightly tapered segment instead of placing the nozzle right at the end of a bend, as this helps produce a more well-formed air ject.

Also found this really cool video series from NeedItMakeIt regarding ducts: [this](https://www.youtube.com/watch?v=1pMJQetyA4A) and this [this](https://www.youtube.com/watch?v=jC5yuF9fMp8&list=PLQzIeH3L1tsXJd5ccb0gNgEOIvACHzmi5&index=22) are the two most useful ones.

 As I wrote yesterday, CarVax recommends not using CFD, and same with Colpher (aka James Pray on youtube, whose video I just linked). But, MetricsTonofCooling, whose designs Ocho recommend I look at, said this:
>For me, CFD was necessary in many ways. Tube fill, upper tube air speed, lower tube air speed, nozzle air speed, and most important, air direction of the nozzles. Aiming (angle)of the nozzles themselves won't change air direction much. Most of that work is done preceding the exit orifice. It can be quite challenging to design a duct. Most of which the problem, mostly with high speed, is the dwell time over the part needing to be cooled as well as part of the model that needs to be cooled when the toolhead is not directly over it. I have two types of ducts: UFO-N-Ator and VaLvNaTor. One is a ring with 4 ports aimed at the nozzle, with a doughnut/plenum feeding the orifices. The second is a duct with valves in them, like a car engine, that spray air outside the model and 2 ports that aim at the nozzle. Both ducts work, but I tend to want to use the UFO over the valve duct. The UFO duct is high velocity air and the Valve duct is high volume, low pressure. If you want to get into such a thing, be ready for pain. What you think will work seems to be opposite, so make a crappy one that you don't think will work 1st, LOL. There is no CAD available for VaLvNaToR (.stl only) and .step or .stl for the UFO duct. I believe there is a mistake in the export of the UFO duct listed below. For some reason when exporting, there is a piece missing in the body or blocked, can't remember which, but the .STL's don't have that issue.
[-UfO-N-AtoR- Duct by XrocksaltX](https://www.thingiverse.com/thing:6779529)
[VaLvNaToR V2 VZ 235 duct by XrocksaltX](https://www.thingiverse.com/thing:6313653)

I think I'll use CFD, but the main conclusion I've drawn from all of my duct research would be that it's very important to prototype and test the fans empirically. So I think the best approach would be to deal with all of the other parts first and leave the toolhead for last, as I don't know how much time that will take, and as it's basically the most important assembly of the whole printer I want to do it well. It's better to finish everything else now, and that way I can spend as much time on the toolhead as I want without having to stress about the rest. It's not like I'll be able to design anything good before actually getting the parts and testing anyway. 

New version of the Z motor mounts:


Those long horizontal semi-circle indents exist so that I can slot in the M3 screws, as the heads wouldn't fit in otherwise. 


I could have used a longer screw and had the screw head hole smaller and thus higher up (as it wouldn't interfere with the pulley cutout space), but well I'm already using 20mm M3s in this build so why buy another size. I can always change this later on if need be.

## Entry 12
- ID: 4886
- Author: AethelVeritas
- Created At: 2026-01-12T19:09:00Z

### Content


Currently the idea would be to use some heat inserts and screws to mount a Z belt clamp to the end of the grey part protruding backwards, but I feel like that would not be optimal at all, and most importantly too weak. I was thinking of maybe having that part encase the back of the motor for extra strength or something.

I again asked in the Ice Cream Factory discord for advice, and Ocho responded suggesting using an aluminum motor mount as well as flipping the Z rails to the front of the extrusions and bolting the extrusion directly into the carriage with M3s. 


Ocho suggested an interesting setup, but doing something like this would mean that I can't run the belt through the bottom slot of the 2020 extrusion like the stinger does it, and that would make things more regarding the X belt path. And also it's a lot more complicated because I have to drill and tap those m3 screw holes as well as a larger slot for the belt. 

Inspired by that, I thought about doing something like this:

One end of the belt is secured into that slot and the other end in a similar slot above, and then the like parallel outer half of the belt would be in front, but obviously that be impossible because of the extrusion, which cannot fit between a belt on standard pulleys. 

Another idea is have the blue part run right in the middle of the belt, as the latter being 9mm and the standard pulley pitch indicating that the minimum distance between the parallel halves would be about 10mm if I thin that section out a bit I should have it.

So roughly something like this:



## Entry 13
- ID: 4887
- Author: AethelVeritas
- Created At: 2026-01-17T23:13:00Z

### Content




Made the Z motor mount from scratch (for the third time). The belt path is now centered on the center of the out most channel in the vertical 2040 extrusion. I also changed the positioning of the leftmost bearing in order to save space. I'll have to update the super derive remove model to a press fit. 


Also finally designed the Z tensioner. Being dumb, at first I forgot about how I centered the belt path on the outmost channel and so when I made tensioner I centered it on the center of the 2040, so I had to redo it. It's blocky, and unnecessarily large, but for now it'll do. In the future I'll optimize it a bit.

## Entry 14
- ID: 4888
- Author: AethelVeritas
- Created At: 2026-02-24T08:05:00Z

### Content

Long time no see. Took a break from the printer in order to finish up some past projects and because I kind of felt 'blocked'. Back at it now, anyway.

Today was mostly about reworking the Z axis, yet again. So I have 3 versions of the bottom Z drivetrain currently, as shown in the past journals, but V3 still had like a lot of unnecessary space in for the 20T small pulley that's drives the main belt, so I messed around with it for some time until I reduced that so it'd only fit 2 x 1mm shims and the pulley itself, plus a bit of tolerance. I'm really learning a lot from my mistakes every time I do one of these reworks, especially how not-parametric I make my parts sometimes. Anyways here's a before and after.


I also finally made the heat insert holes for the top pulley "cage" clamp. I've decided I'll be using the M3 x 5.7 inserts throughout as much as possible of my build, so the holes were made per [this](https://www.prusa3d.com/product/threaded-inserts/) spec. 

Also, I finally figured out belts! Was kind of tedious as I couldn't wrap my ahead around the featurescript but after rummaging through the internet for a bit I figured it out!

I'll obviously change the thickness later on but it's finally starting to look more and more like a legitimate printer. Adding belts also helped me notice that my calculations regarding the offset of the top and bottom Z pulleys relative to the vertical extrusion were off:

This I soon fixed, and now it's looking much better. I'm happy with the bottom Z drivetrain, but not with the tensioner, so I'll probably rework that tomorrow. 



## Entry 15
- ID: 4889
- Author: AethelVeritas
- Created At: 2026-02-25T07:14:00Z

### Content





Made a new version of the tensioner, and also added some slots to make it look nice reduce material waste. I'm still a bit unsure about how thick I should make everything though...I mean 6mm is kind of thick for walls that don't have any direct tension applied to them and just act as guides.

## Entry 16
- ID: 4890
- Author: AethelVeritas
- Created At: 2026-02-26T07:45:00Z

### Content

Last journal post was for yesterday. I've slept on it and realized that my idea was dumb. Adding slots does not reduce waste in this case: it just makes the part have more perimeters in the slicer, which only increases both print time and material waste. Also, I should optimize it's length given the belt tensioning formula Deadlock gave me a while back (the one I alsu used for the Y axis. Now that I added a Z belt to the assembly two days ago I can make a pretty decent estimate of how long the belt will be, which in my case is 375 mm from top to bottom (so the actual belt length would be doubled in real life, but that doesn't matter for the calculation). 379(+ 4 mm wiggle room) * 0.02 gives 7.58, and I'll just round that up to 8 mm. So I should be able to tension 8 mm. Tensioner block is 25 mm tall, so 34 mm slot height. Wait no I can't have the tensioner just hanging out. Add 7 mm to that. 


Ok this is what I'm going with for now. In the future I might remove the screw on the side as well as one of two top screws that hold the top X extrusion to the Z axis and then just use a longer similar screw to directly bolt tensioner through the top X and into the Z extrusion. Should be stronger, but I'll see. 

I've also decided to drop the 48v dream. TMC5160 Pros are prone to blowing/overheating as I recently learned in the Monolith discord, and I'd have to get 4x TMC5160 Plus, which would be like a fifth of the whole budget, $80. And I just realized that belts are actually more expensive than I thought, so yeah no can do 48v. Plus I talked to Renovic and also watched some older videos of Kevin's Kevender while it was still on 24v and they can hit like pretty decent accels and speeds even with 24v. Nothing like the 700 mm/s speed or 1000k accels that LH stinger can, but well then again my Q1 Pro usually prints at like 300 mm/s and it still seems really fast for me. I'll just focus on a good 24V base build, one that I can either upgrade to 48V in the future or reuse the parts for a 48V corexy. We'll see. I have to stop trying to overachieve...a bird in hand is worth two in the bush, and I really have to finish the damn printer already.

At this point I should make a more detailed rough BOM. 
https://docs.google.com/spreadsheets/d/19SDQH5rKj-VOt543ikEq3R2ylwxd--UoErljUox35hg/edit?usp=sharing

So, according to the Ice Cream Factory's Discord:
- Trianglelabs is the cheapest decent option for belts, and I can also get pulleys from there
- According to deadlock, for live idlers: "g6 is preferred here, h6 is still good but will require more work as clearance goes down to 0), and press fit on the housing (M7, N7)."
- Raindew bearings, make sure they are 2RS
https://docs.google.com/spreadsheets/d/19SDQH5rKj-VOt543ikEq3R2ylwxd--UoErljUox35hg/edit?gid=0#gid=0

Here's what I've got so far, and I still need a 340mm 2040 extrusion, lube for the rails, T-nuts, screws, 80T pulleys + timing belts (x 2). I've pretty much scrapped JLCMC because it turns out that shipping from there costs like $34, which is crazy. I also still need a Klicky probe, fans for the hotend + the motherboard, wires+crimps, and also brackets for the Y 4040, as I'll be shifting in front.

## Entry 17
- ID: 4891
- Author: AethelVeritas
- Created At: 2026-03-10T06:09:00Z

### Content

Ok I'm making the toolhead for #rework, can't fit in the budget. Brazuka gave me an updated quotation for the rails, which would be 87 (4x 300mm Z1 and 1 x 300 Z2) + 24 shipping, and then I just realized I actually can't use only my 350w psu cause the bed draws like 240W max and the Dragon hotend like 90-115W if I don't go for the volcano option. I really don't want to buy another 24v PSU for nothing, so I guess 48v it is. I'll just buy some TCM5160 Pros and it is what it is. I've got crimps and wires for everything I think, so I just need to get some wire sleeves as well as maybe a buck convertor.

Ahhh scratch that. Been racking my head with electronics and how'd I'd deal with them for the past 5 hours (not going to add that though because I didn't really journal it). Ok so I've decided that I'll let electronics be for the moment. I'll build an ebox for a either stasis or rework (I found some really cheap 3-4mm plexiglass and I want to make this really good looking transparent sides ebox), and I'll buy the 5160 drivers with that grant, and the PSU as well. I'll just focus on refining and making what I've designed so far better and just hope the reviewers see the amount of work I've put into this. Man I hate compromises! 



Made some rail endstops, mock plexiglass panels, and also messed around with an octopus pro and pi 3b+ to see if I can fit them on the bottom. Octopus is too long to put like parallel to the base with the ethernet ports like in the front, so the only way I'd be able to make it fit would be to rotate it 90 degrees and place in the center, and then like direct everything else from the Pi, whose ports would be accessible. Honestly this sounds feasible enough so I might actually do that. 
But then again, did some more ebox research, and turns out that doing that without something like LH's breakbeat board isn't that hard either. In fact, in his build log, the latter uses some of those blank pcbs and some JSTs in order to improvise one https://github.com/lhndo/LH-Stinger/wiki/Build-Log#wiring. 
Zwirbel from the Stinger Discord recommended that I get some of these connectors if I plan to do so. And I'd need longer wires obviously, but I don't think that's gonna be a problem. 

## Entry 18
- ID: 4892
- Author: AethelVeritas
- Created At: 2026-03-11T07:51:00Z

### Content

Polished up the readme, assigned some new colors, changed the name, and mainly just finished the BOM. LH's [Stinger BOM](https://docs.google.com/spreadsheets/d/1s8ulLfThmbuy1G_40MvkXXL2oVx9PZhvpAY9hMxqYbg/edit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) was very useful, as it contains links to reputable sources. 


## Entry 19
- ID: 726
- Author: AethelVeritas
- Created At: 2026-03-30T17:56:31Z

### Content

So last time I took tackled the ebox idea, I ditched in favor of mounting two psus of the same size on the back of the Z extrusions. Now I'm going for ebox, thanks to extra possible funding. What I'm getting at is that I don't need my 48V PSU to be the same size as the 350w 24v I'm getting off of the Ender. Never mind that, 350w it is. It's cheap ($20), and it should suffice for a CoreXY. Why are drivers so expensive :((. Gonna have to shell out $86 on 48v drivers. Turns out 5160T Plus have better cooling and thus are less prone to frying as compared to the slightly cheaper ($18 less) 5160T Pros. Mounting them is going to be interesting though.

Spent some time finding some accurate models for the pi, drivers, and octopus pro and then imported them into Onshape. Messed around with them in an assembly to get a rough idea of how I want to position them.



I think I'll be going with something like this, with the drivers on the bottom. Yes this will make the ebox wider, but it's still pretty compact (probably <15cm with the walls included) and this also allows me to do an interesting lid idea I had. 

I want to make the slanted part have a small acrylic window, and add fans to the bottom vertical part for cooling. Also, I was thinking of maybe using some alu hollow rods for the frame, as they are pretty cheap, would look cool and would maybe give my structure some more stability. We'll see. Oh and I also spent some time making a mount for the octopus pro (obviously not finished yet). 


### Recording Links

- https://lookout.hackclub.com/api/media/f7e4fa06-7d14-4743-97c6-4d976468209f/video.mp4

## Entry 20
- ID: 1050
- Author: AethelVeritas
- Created At: 2026-04-03T17:53:52Z

### Content




So messed around some more in CAD, and this is what I think I'll go with. I can have the 6025 fans on the top on the outside to save space, stacking two TMC5160 Plus drivers allows me to save space lengthwise, and I'll add some cutouts in the bottom to improve air circulation. Still very cramped though unfortunately. I left 5 mm space between the PSUs, hopefully that'll be enough. 

Ok talked to LH and someone else in the LH stinger discord, and turns out my idea of stacking them isn't that great. Turns out that most of the heat from the drivers dissipates on the bottom, not the top where you usually see the heatsink. Seemingly, BTT has a history of not placing their heatsinks correctly. 



Ocho from the Ice Cream Factory Discord suggested I rotate them vertically, and this seemed like the best option, but after some more back and forth I've come to the conclusion that it'd be too cramped, and that I'd have to make the Ebox too big to get proper cooling. 


Seems I'd want about 20mm between the PSUs for instance, and 20-35mm between the drivers and mainboard for wiring. After much messing around with positioning and research, I think I'll have to give up the Ebox idea. I just can't get good cooling without making a humongous box, which besides not being printable for anyone with an ender who might want to use it in the future, would also consume a tremendous amount of filament. It's sad really: I had this great idea of a good looking box with transparent plexiglass cutouts and all, but it is what it is. Ocho reminded me that I don't actually need a new PSU like I initially calculated the last time I considered giving up 48v for now, because I can just get a 15-20 dollar AC bed heater and wire it directly to the power socket basically, meaning that I don't have the bed draining 230W from my 350W PSU. 

Yes I'll be sacrificing a lot of speed, but honestly I don't really want a very fast (500mm/s) bedslinger...not that efficient and not that interesting honestly. I'll still be able to hit good speeds (like 300/400mm/s), which is more than enough, due to my AWD setup. And honestly I've kind of got burnout from this project: it was meant to be a quick printer so I can get parts to build a good one, a corexy. I've sunk too much time in a bedslinger. Time to wrap it up and actually build the thing. 

### Recording Links

- https://lookout.hackclub.com/api/media/fb5e4a1a-39d1-4671-bb90-40f25136ad30/video.mp4

## Entry 21
- ID: 1557
- Author: AethelVeritas
- Created At: 2026-04-09T08:30:32Z

### Content

More research. AC might not be feasible after all because it's dangerous. I need to ground the frame, have a GFCI outlet, etc. And all of that stuff adds up. The whole point of going with the AC bed heater was to minimize cost. But if it's gonna cost like $100 dollars for something like that then I'd prefer to just get 5160s and a 48v for that sum, as I can reuse those later  and I'll get more speed. 
However, I think it'd be wise to make an updated version of my whole BOM first. Better get it over with it now and make sure I don't design something for nothing. 

So basically all I've done today is getting started on the BOM and thinking more about what items I could reduce/get a different part to optimize cost.



### Recording Links

- https://lookout.hackclub.com/api/media/e082c6bd-16ad-4b2f-b8c8-f379e4956d57/video.mp4

## Entry 22
- ID: 1679
- Author: AethelVeritas
- Created At: 2026-04-10T19:14:37Z

### Content

I think I'll have to return (once again) to the Ebox idea. Can't think of any other way, and as I previously mentioned AC seems too dangerous, especially with a moving bed. Also, I'm almost certain that I won't be able to get a filament sponsorship from Polymaker, as May and several who are building printers for #infill were rejected (and those were good unique projects). This is unfortunate, as I was kind of "relying" on that for filament. So now I'll have to somehow squeeze one-two rolls of PET-CF/ABS/ASA in the budget. I'm getting uncomfortably close the $600 mark, and I still don't have a hotend.

Found a 500x500 4mm plexiglass/hobbyglas sheet for 9 USD at a local hardware store. Transparent as well as black/color options, and rated up to 75C. A quick search shows that motherboards+drivers shouldn't usually exceeed 45-55C (I am not certain how accurate this estimate is though). I think I'll use this for panels if I can find a good way to cut it. I've got a router, so I guess I could use that for cutting slots for ventilation, but it seems this more brittle then acrylic, so I am not certain how well that would work. 


All my panels would fit easily though. 

For reinforcing the frame, since I'll be using plexiglass panels instead of 3D printing everything I was thinking of using alu pipes, as they are really cheap, I can source them locally, and I've used them before for a telescope mount. They're like $2-3 for 1000mm x 8mm x 1mm (thickness). Thing is I'll have to consume more material to make panel mounts. Not that that is a great problem by any means, but it makes mounting components and stuff harder. Now the other alternative I've been considering is just getting some alu extrusions. I found a listing on Aliexpress for 4 x 330mm 2020s for about $25. The one 2020 I had in my BOM previously that I was planning on using for the gantry is $9 for reference. Thing is, I'd have to get that as well as the gantry one, and I'm not sure if the price is worth it. Like $25 for an ebox frame? Seems a bit overkill. I guess I'll figure the layout first and then worry about the frame.

So...cooling. Found a message in the Monolith Discord by Vex saying that external drivers do not really need cooling. Also while browsing I noticed that a lot of builds (including Brazuka's) don't actively cool the mainboard. Interesting. Maybe I'll just add a large PC fan for airflow since my Ebox is smaller than a Trident's electronic bay for example. Why do I have to overthink literally everything. This perfectionism is going to be the ruin of me.

Hopped on a huddle with Renovic and some other people later on in the day, and decided that the 3mm plexi panels should be enough. Also talked to LH who said he used a 4020 noctua blowing on the PSU fan in order to make sure it doesn't overheat in the summer (because the octopus pro covers part of it. 

### Recording Links

- https://lookout.hackclub.com/api/media/80a5dd69-92e4-4a9b-8f17-06549a28e744/video.mp4

## Entry 23
- ID: 1695
- Author: AethelVeritas
- Created At: 2026-04-10T21:27:11Z

### Content


Made a rough mount for the drivers. Also did a bit more research on how flimsy those 3mm panels are. From what I've found, they appear to be PVC, and not very flexible but definitely not rigid. I'm still debating whether I should go with 4mm transparent plexiglass or use those 3mm PVC ones. 4mm seems more rigid and solid, but cutting and post processing might make it look worse. I think if I can cut it at my local library I'll go with the plexiglass. To be honest a mostly transparent ebox with maybe some cool leds inside would look pretty darn sick. Also researched fans a bit again. I might add a 120mm fan one end to help circulate the air, but I don't think I'll add any other fans besides that. Asked in the monolith discord and most people don't use active cooling for their 5160 plus drivers, only for stepsticks. So I guess the like $15 difference between the stepstick and these externals is now worth it, because besides getting better quality I'm also "saving" on the fans. 

### Recording Links

- https://lookout.hackclub.com/api/media/3d24d85b-8ba4-4b45-b696-592677f41106/video.mp4

## Entry 24
- ID: 2221
- Author: AethelVeritas
- Created At: 2026-04-14T18:49:45Z

### Content

One of the reviews on that 4mm plexiglass I was looking at said it was really easy to bend with a little bit of heat....what if instead of cutting like the angled front cover I bend it. Scope creep is real haha. 

After some more CAD, here's the rough idea. 



Now my initially idea was that I'd have braces such as the red part all along the frame, to compensate for the fact that I can't print the frame in one piece.




I was planning to drive M3/M2 screws through the outside frame and the panel and into heat inserts/nuts secured in these braces. But now I realized that firstly it would consume both material and space for not that much of an addition to rigidity. I kind of keep forgetting that this is actually a really small box, and hence the rigidity of the panels will be pretty dang high, especially if I go with 4mm panels. Now, my outer frame will actually be thick enough that I can put the heat inserts in the frame from the _inside_, and screw the screws from the inside, thus completely hiding them. 

I'm also debating how I'll split the frame. I could split it directly in half, like this:


But the issue is that I'll lose some rigidity on the longest side. I guess the panels could compensate for that, but I'm not sure. 


Well this is how it's looking so far. Not bad in my opinion. I've started adding the holes in the panels and the frame for the heat inserts and screws, but that's gonna take some time. Very tedious unfortunately. I really hope I won't have to rework this. 

### Recording Links

- https://lookout.hackclub.com/api/media/80767ab6-3c3b-4414-a494-b438d9c049d6/video.mp4
- https://lookout.hackclub.com/api/media/239cd98c-8f8d-4a27-a1d4-2de468122cfb/video.mp4

## Entry 25
- ID: 4893
- Author: AethelVeritas
- Created At: 2026-05-02T05:16:20Z

### Content

Project transferred from Blueprint! Duration Transferred: 132.0h

## Entry 26
- ID: 8022
- Author: AethelVeritas
- Created At: 2026-05-19T19:15:27Z

### Content

Worked on the ebox again...man I hate this thing. Why do I have to over-complicate everything. Anyways I made screws holes to attach the panels to the frame, and it was one of the most tedious things I've done in quite some time. I think I'll stick with black 3mm panels for the sides back, and bottom, and then just use 4mm clear plexiglass for the front. Honestly should have just made everything except the front cover printable...would have saved a lot of screws and post processing. Well anyways hopefully this'll reduce material cost by a bit, even though it's only like $10-20. I'll derive the panels (which now have screw holes) in another part studio, cutout the centers, and then use those as cut and drill guides for the plexiglass. Cut some yesterday for another project using the same technique and it worked quite well. 



### Recording Links

- https://lookout.hackclub.com/api/media/66992d0c-a727-4ef4-b635-bd78e4f1ab3b/video.mp4
- https://lookout.hackclub.com/api/media/5ce17cff-c9dc-42fe-8e92-643b7abe586d/video.mp4

## Entry 27
- ID: 8513
- Author: AethelVeritas
- Created At: 2026-05-22T18:16:46Z

### Content




So first of all, I've added magnet holes for the door. While for the door frame I'll just be gluing them in, as you can see in the last pic, for the frame I've also managed to make them slot in. Hopefully the 0.8 mm of plastic will be enough to keep them from popping out but at the same time not weaken their strength. 

Then I moved on to the hinges:



As you can see, I've used the LH stinger's Ebox hinges as my main reference, and I've only changed the dimensions slightly for my use case. A piece of filament or wire will go in the small "pin hole". 


Then I finally started making the main assembly. I've decided I'll only use clear plexiglass for the door, as it has a tendency to gather a lot of oil and marks. I'll use 3mm polycarbonate for the rest of the walls. 





Also, I modifed the psu mount I had created earlier to also hold the raspi 3, and added some cable channels on top near the mainboard as well. These are from the LH Stinger, with just the logo removed. I'll have to make a logo and add it somewhere on the ebox once I finish renders and the BOM and everything. I still have to make its feet (I want to use the same kind of rubber feet as I'll use for the Y-axis, to save money) and holes/an inlet or outlet of sorts to let the cables pass in, as well as a mount for the power inlet and switch. I'll be drilling holes in the walls for ventilation, which is another reason for avoiding the plexiglass for all walls, as it being transparent kind of makes the hole burrs more nagging to the eye.. 

### Recording Links

- https://lookout.hackclub.com/api/media/513a9f47-bd40-4e23-955a-99457558040d/video.mp4
- https://lookout.hackclub.com/api/media/cb79d077-c574-4f93-89b5-27c0ce9ff9cb/video.mp4

## Entry 28
- ID: 8876
- Author: AethelVeritas
- Created At: 2026-05-24T14:39:35Z

### Content




Made the power inlet/cable outlet mount today. A bit overkill, and bit complicated, but I also made an inner piece because since I'll be cutting the panels by hand with a drill and a small saw I can't really cut complex shapes precisely, so they'll be rough, and since that area will be clearly visible through the door I thought I should make it look nice. 


Also spent some time adding finishing touches such as all the screws and the "clamps" for the driver mounts. I still have to deal with ventilation, which is going to be an immense pain. The amount of time I'll waste drilling holes in those panels will be insane. Also, I'm kind of worried, as I've now realized that the distance between the edges of the panels and the holes is like 1.7 mm or something like that...not good. I'll fix that later I guess. 

### Recording Links

- https://lookout.hackclub.com/api/media/5a5297f3-a69c-422c-a182-8976489d47f0/video.mp4

## Entry 29
- ID: 9165
- Author: AethelVeritas
- Created At: 2026-05-25T18:03:30Z

### Content





Ventilation! Finally. This didn't turn out as detailed as I'd initially hoped, because I'm running out of time. Hopefully it'll be enough. I'm thinking that worse case scenario I can just open the door when printing. Using a 6040 fan that will hopefully draw the air from the above the drivers (which I think will be letting off the most heat), allowing new cool air to flow in through beneath the holes beneath the drivers and on the left side of the ebox. 



I also made a new modified version of the gantry in order to give the custom toolhead I designed (Aeolus) more X travel. I think the whole gantry looks even cooler now honestly
. 



I also made a dock for the quickdraw probe, based on the LH Stinger's dock. As you can probably tell, I'll be losing some X print space because the bed is too big and the gantry too small for the current toolhead to have space to get lower than the bed in the Z to attach to the probe. 

On a side note, I've been thinking of renaming the whole project "Revenant". A revenant is someone who returns after a long time, usually from the dead, so I guess this would still kind of fit the theme I'm trying to go with here: a "reborn" Ender. But we'll see. I kind of like the current color scheme. 

### Recording Links

- https://lookout.hackclub.com/api/media/580312b1-8756-4319-8427-3feff466f974/video.mp4
- https://lookout.hackclub.com/api/media/87b42c9e-3e14-4fbd-91a2-0d2a52f2ddc7/video.mp4

## Entry 30
- ID: 9447
- Author: AethelVeritas
- Created At: 2026-05-26T19:02:44Z

### Content



Started off with these logos I found on the web as inspo. I especially liked the last one, but I want to keep the geometry simple. Messed around with some logo generators for like about an hour, and this is the one I eventually settled on:

Made a bitmap in inkscape, exported it as svg, converted it to dxf, and then I added to the CAD.  Made these 4040 endcaps with the logo on them....I'll use a lot of z-hop to print two different colors on the base layer. Also made a larger phoenix that I'll glue to the back of the ebox. 


The rest of the time was spent just adding different missing screws in the assembly and working on the BOM. 

Stuff I have left to do:
- Finish BOM. 
- Polish up README writing.
- Generate/make some pics/drawings for the main pics. 

### Recording Links

- https://lookout.hackclub.com/api/media/64f2eeed-c9ef-452d-90c6-6257922ca035/video.mp4
- https://lookout.hackclub.com/api/media/e0f8519f-be4e-44a1-8307-6fe0b647673f/video.mp4

## Entry 31
- ID: 10232
- Author: AethelVeritas
- Created At: 2026-05-29T19:42:46Z

### Content

Worked on the BOM. I hate this part honestly...very tedious and so many little things that can go wrong. Not much I can journal about that, but some things I learned are:

1. Add every part to a final assembly, and use as much standard content as possible. I use Onshape, and it can generate a BOM of an assembly, which is very helpful. Using as much standard content as possible ensures Onshape also displays names+dimensions of screws, nuts, washers, etc. 
2. After making a final assembly, open the generated BOM and try to see if you can't reduce different instances by using the same kind of screw for example. Let's say I need 20 M3 x 6mm screws, and then use 4 M3 x 8mm screws for some other part. If I can modify the latter to use 6mm screws, I might have just saved $4, which is about the minimum price for a bunch of screws off of Ali. 
3. If you can't reduce different instances as mentioned above, check local stores' websites. If a find a screw I only need 4 of for several cents at my local hardware store then I don't need to order it. Double check though, because it's really annoying when all your parts arrive only for you to realize you can't source X part locally as you thought. Waiting another several weeks for stuff from Aliexpress to arrive is not fun. 

Here's a pic of how I've structured my BOM. One thing which rather confused me was quantity. Like if need 4 fasteners, but they only come in a 10 pack for $5, then do I add another column to the BOM saying the quantity and then list the price for a pack of 10? Wouldn't that be confusing as I'd think I have to buy 4 packs of 10? So for now I've just "ignored" quantity. I've specified the number of pieces  in the title, and then listed the final price for all pieces. There's probably a better way to do this, but for a hobbyist level this should be fine. I've looked at other BOMs from other hackclubbers who are more skilled in the art of 3D printing and they seem to be doing the same. 
Oh and also I must say that [LH Stinger BOM](https://docs.google.com/spreadsheets/d/19SDQH5rKj-VOt543ikEq3R2ylwxd--UoErljUox35hg/edit?gid=0#gid=0)
was huge help for referencing reliable sellers of screws and the like. 

Another issue I faced was sourcing filament. I really wanted to get good ASA, since I can't use PET-CF (can't anneal it). The problem is most brands were either expensive or didn't have a decent fiery orange. I looked at Extrudr, Polymaker, 3DJake, Sunlu, and many others. In the end, after scouring some Discord servers I settled on Torofil from toro3d for the black and then just sourcing some orange locally, either Polymaker Polylite or Devil Design ASA. I really wanted to get torofil because it's pretty highly recommended on the Monolith Discord, and it's maker/owner of toro3d is pretty active there. And of course because one spool of black ASA costs only 19 euros on his website right now, which is like Elegoo levels of cheap.

Moving on to the biggest thorn in my side: rendering. At first, I tried Blender. Wasted like an hour on that before giving up: I knew there was no way my Intel iGPU could handle a 1.3 GB .obj file, but thought I'd try anyway, as I didn't really see any other way. My laptop felt like it was about to explode when Blender crashed. I also considered making a drawing style main readme pic like I did for the  [Aeolus](https://github.com/AethelVeritas/Aeolus), but unfortunately my laptop again couldn't handle it. Onshape was slow and laggy when trying to load views in the drawing, the lines were too choppy/large to properly show off all the detail, and I also didn't want to spend half a day learning how to use the drawing workspace properly just to get some mild looking pics. Fortunately, Raygen reminded me on the HC Slack that Onshape has a free 6 month trial for professionals, which also grants access to the built-in renderer. So I made a new account, claimed the trial, and started to mess around with said renderer, which is honestly awesome. Pretty intuitive, nice UI, and not too laggy. The problem is I don't really know what I'm doing, and I'm also a perfectionist. I don't know why I want pro level renders...many quality 3DP projects have almost stock renders. I think I might be focusing too much on this point..this isn't something that I intend to commercialize, like the LH stinger for example. Anyways, an annoying thing I learnt is that if you use composite parts in an assembly, you then can't assign appearances to individual parts, only to faces. This is really frustrating because now my motors are pretty much stuck with the default/auto appearances, which look like shit. But oh well, lesson learned. Oh and also something I wanted to do is use the github dark theme background color as my background color, so that the render would blend in with the background of the readme. Seems to have worked out pretty well....anyway here are some random renders.






### Recording Links

- https://lookout.hackclub.com/api/media/fb0c7484-fd64-464c-a21f-4fd26ecbb88e/video.mp4
- https://lookout.hackclub.com/api/media/f36aa8f8-c1c5-4730-a882-70274208454c/video.mp4
- https://lookout.hackclub.com/api/media/97e499c7-b17a-406d-8926-9329ce2ddfb3/video.mp4

## Entry 32
- ID: 10867
- Author: AethelVeritas
- Created At: 2026-06-01T10:30:37Z

### Content

Not much to say. This was mostly polishing up stuff, making a rough firmware file, ebox wiring diagram, and the zine. I forgot how much I hated making these kind of posters honestly....I am just not good at art of any kind. Actually, I'm just as good as I need to be to tell that what I'm doing does not in fact look good haha. So yeah, made the zine, made some more renders and finished up the readme. 


### Recording Links

- https://lookout.hackclub.com/api/media/72323eed-ef79-446a-8280-71ada5dd8172/video.mp4
- https://lookout.hackclub.com/api/media/10f4bcd8-23c3-45b2-9d93-af3e1e9e1264/video.mp4
- https://lookout.hackclub.com/api/media/c8aabee5-d1ce-4ecf-ad80-59d94d0ee90d/video.mp4
- https://lookout.hackclub.com/api/media/c55da64b-201d-4f46-9132-15f5e37acf2d/video.mp4

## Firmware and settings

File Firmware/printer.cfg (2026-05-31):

# ===========================================================================
# Phoenix
# ===========================================================================
 
[include fluidd.cfg]
[include quickdrawprobe.cfg]
 
# ---------------------------------------------------------------------------
# MCU
# ---------------------------------------------------------------------------
[mcu]
# Find your serial path with: ls /dev/serial/by-id/
serial: /dev/serial/by-id/usb-Klipper_stm32h723xx_CHANGEME-if00
restart_method: command
 
# ---------------------------------------------------------------------------
# PRINTER
# ---------------------------------------------------------------------------
[printer]
kinematics:             cartesian
max_velocity:           500
max_accel:              20000
max_z_velocity:         20
max_z_accel:            500
square_corner_velocity: 8.0
minimum_cruise_ratio:   0.5
 
# ---------------------------------------------------------------------------
# X AXIS
# ---------------------------------------------------------------------------
[stepper_x]
step_pin:               PF13
dir_pin:                PF12
enable_pin:             !PF14
rotation_distance:      40          # Calibrate: 20T GT2 pulley = 40mm
microsteps:             16
full_steps_per_rotation: 200
endstop_pin:            PG6
position_endstop:       0
position_min:           0
position_max:           220         # Update after measuring actual travel
homing_speed:           60
homing_retract_dist:    5
 
[stepper_x1]
step_pin:               PE2
dir_pin:                PE3
enable_pin:             !PD4
rotation_distance:      40
microsteps:             16
full_steps_per_rotation: 200
 
[tmc5160 stepper_x]
cs_pin:                 PC4
spi_software_miso_pin:  PA6
spi_software_mosi_pin:  PA7
spi_software_sclk_pin:  PA5
interpolate:            False
run_current:            2.0         # Update 
sense_resistor:         0.075       # Update to actual 
stealthchop_threshold:  0
 
[tmc5160 stepper_x1]
cs_pin:                 PD11
spi_software_miso_pin:  PA6
spi_software_mosi_pin:  PA7
spi_software_sclk_pin:  PA5
interpolate:            False
run_current:            2.0
sense_resistor:         0.075
stealthchop_threshold:  0
 
# ---------------------------------------------------------------------------
# Y AXIS 
# ---------------------------------------------------------------------------
[stepper_y]
step_pin:               PG0
dir_pin:                PG1
enable_pin:             !PF15
rotation_distance:      40
microsteps:             16
full_steps_per_rotation: 200
endstop_pin:            PG9
position_endstop:       0
position_min:           0
position_max:           220         # Update after measuring actual travel
homing_speed:           60
homing_retract_dist:    5
 
[stepper_y1]
step_pin:               PF11
dir_pin:                PG3
enable_pin:             !PG5
rotation_distance:      40
microsteps:             16
full_steps_per_rotation: 200
 
[tmc5160 stepper_y]
cs_pin:                 PD14
spi_software_miso_pin:  PA6
spi_software_mosi_pin:  PA7
spi_software_sclk_pin:  PA5
interpolate:            False
run_current:            2.0
sense_resistor:         0.075
stealthchop_threshold:  0
 
[tmc5160 stepper_y1]
cs_pin:                 PC6
spi_software_miso_pin:  PA6
spi_software_mosi_pin:  PA7
spi_software_sclk_pin:  PA5
interpolate:            False
run_current:            2.0
sense_resistor:         0.075
stealthchop_threshold:  0
 
# ---------------------------------------------------------------------------
# Z AXIS 
# ---------------------------------------------------------------------------
[stepper_z]
step_pin:               PG4
dir_pin:                PC1
enable_pin:             !PA2
rotation_distance:      40          # Adjust 
microsteps:             16
full_steps_per_rotation: 200
endstop_pin:            probe:z_virtual_endstop
position_min:           -5          # Allows Z offset calibration below 0, watch out
position_max:           250         # Update after measuring actual travel
homing_speed:           10
second_homing_speed:    3
homing_retract_dist:    5
 
[stepper_z1]
step_pin:               PF9
dir_pin:                PF10
enable_pin:             !PG2
rotation_distance:      40
microsteps:             16
full_steps_per_rotation: 200
 
[tmc2209 stepper_z]
uart_pin:               PC7
interpolate:            False
run_current:            0.8
stealthchop_threshold:  0
 
[tmc2209 stepper_z1]
uart_pin:               PF2
interpolate:            False
run_current:            0.8
stealthchop_threshold:  0
 
# ---------------------------------------------------------------------------
# EXTRUDER 
# ---------------------------------------------------------------------------
[extruder]
step_pin:               PC13
dir_pin:                PF0
enable_pin:             !PF1
rotation_distance:      4.637       # Calibrate with e-step test after setup
microsteps:             16
full_steps_per_rotation: 200
nozzle_diameter:        0.400
filament_diameter:      1.750
heater_pin:             PA3
sensor_type:            PT1000
sensor_pin:             PF4
pullup_resistor:        4700        # Required for PT1000 on most boards, doublecheck
min_temp:               0
max_temp:               350
min_extrude_temp:       170
max_extrude_only_distance: 500
max_extrude_only_velocity: 60
max_extrude_only_accel: 1500
max_extrude_cross_section: 5
pressure_advance:       0.035       # Tune with PA test after setup
pressure_advance_smooth_time: 0.040
# Run PID_CALIBRATE HEATER=extruder TARGET=250 and paste results here below 
control:                pid
pid_kp:                 28.0
pid_ki:                 2.0
pid_kd:                 90.0
 
[tmc2209 extruder]
uart_pin:               PE4
interpolate:            False
run_current:            0.65
stealthchop_threshold:  0
 
# ---------------------------------------------------------------------------
# HEATED BED
# ---------------------------------------------------------------------------
[heater_bed]
heater_pin:             PA1
sensor_type:            Generic 3950
sensor_pin:             PF3
min_temp:               0
max_temp:               130

# Run PID_CALIBRATE HEATER=heater_bed TARGET=60 and paste results below
control:                pid
pid_kp:                 60.0
pid_ki:                 2.5
pid_kd:                 400.0
 
# ---------------------------------------------------------------------------
# FANS
# ---------------------------------------------------------------------------
[fan]
pin:                    PA8
 
[heater_fan hotend_fan]
pin:                    PE5
heater:                 extruder:
heater_temp:            50.0
fan_speed:              1.0
 
[controller_fan controller_fan]
pin:                    PD12
stepper:                stepper_x
 
# ---------------------------------------------------------------------------
# BED MESH
# ---------------------------------------------------------------------------
[bed_mesh]
speed:                  150
horizontal_move_z:      10
mesh_min:               20, 20
mesh_max:               200, 200
probe_count:            5, 5
mesh_pps:               2, 2
algorithm:              bicubic
bicubic_tension:        0.2
fade_start:             0.6
fade_end:               10.0
 
# ---------------------------------------------------------------------------
# Z TILT
# Adjust z_positions to match where each Z motor drives the gantry
# ---------------------------------------------------------------------------
[z_tilt]
z_positions:
    -50, 110
    270, 110
points:
    30, 110
    190, 110
speed:                  150
horizontal_move_z:      10
retries:                5
retry_tolerance:        0.0075
 
# ---------------------------------------------------------------------------
# INPUT SHAPER
# Fill in after running resonance tests
# ---------------------------------------------------------------------------
[input_shaper]
shaper_type_x:          mzv
shaper_freq_x:          0
shaper_type_y:          mzv
shaper_freq_y:          0
 
[resonance_tester]
accel_chip:             adxl345
probe_points:           110, 110, 20
 
# ADXL345 — comment out if not connected yet
[adxl345]
cs_pin:                 PB12
spi_software_sclk_pin:  PB10
spi_software_mosi_pin:  PB11
spi_software_miso_pin:  PB2
axes_map:               x, y, z
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

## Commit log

2026-03-11 Added CAD
2026-03-11 added BOM.csv
    [BOM.csv]
2026-05-31 center logo test
    [phoenix_logo.dxf]
2026-06-01 Added zine, source files, gallery pics.
    [BOM.csv]
